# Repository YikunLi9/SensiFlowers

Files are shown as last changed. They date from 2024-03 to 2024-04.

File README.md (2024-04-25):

# SensiFlowers

## What the project does?

This project is an indoor artwork that connects with the environment and presents the data to the user in the form of art. The product will collect temperature and humidity of indoor environment through DTH-22 sensor, and display the data using the mechanical flower opening degree and color temperature of rgb light effect.

The whole product consists of three mechanical flowers and a wooden structure, as shown below:

<div align="center">
  SensiFlowers
</div>

The color of each flower in working mode represents a different data environment, with green representing carbon dioxide, red representing temperature, and blue representing humidity. As the ambient value increases, the color temperature will change from light to dark, and the flowers will gradually change from crouching to fully open.

## Why the project is useful?

We designed this project to fill a gap in the artistic emotional value of environmental monitors currently on the market. Most of the environmental data measurement devices on the market, only through a simple digital way, will measure the environmental data to express, which may lack a spiritual aesthetic, difficult to bring users a spiritual level of pleasure. 

Therefore, this product completes the measurement and display of environmental data through the artistic expression form of mechanical flower and lamp effect, and has a certain physical significance and practical value at the same time, it can also be used as an art decoration, placed in the living room or hung on the wall, bringing certain aesthetic value.

## How We Design？

### Initial Concept and Prototyping
The initial design concept focused on integrating natural elements, specifically using the imagery of a blooming flower to represent and interact with environmental data. Initial prototypes utilized thermally responsive metals to simulate the blooming process. However, this approach was found to interfere with the accurate monitoring of environmental conditions, as the device's primary function was compromised by the temperature sensitivity of the materials.

### Shift to Origami Modelling
To achieve a more reliable and aesthetically pleasing design, the development shifted towards origami modeling. This approach aimed to abstractly and artistically replicate the dynamic nature of a blooming flower, enhancing both visual appeal and functional reliability. Initial attempts to implement a hinged mechanism for transformation proved too complex and fragile for practical application.

<div align=center>
  Shift to Origami Modelling
</div>

### Material Innovation
The design evolved through a focus on material innovation. By integrating wooden panels with elastic TPU materials, the device was endowed with the necessary flexibility to mimic origami's bending and folding capabilities without compromising durability. This combination allowed significant bending angles while maintaining a robust structure within each modular unit.

<div align=center>
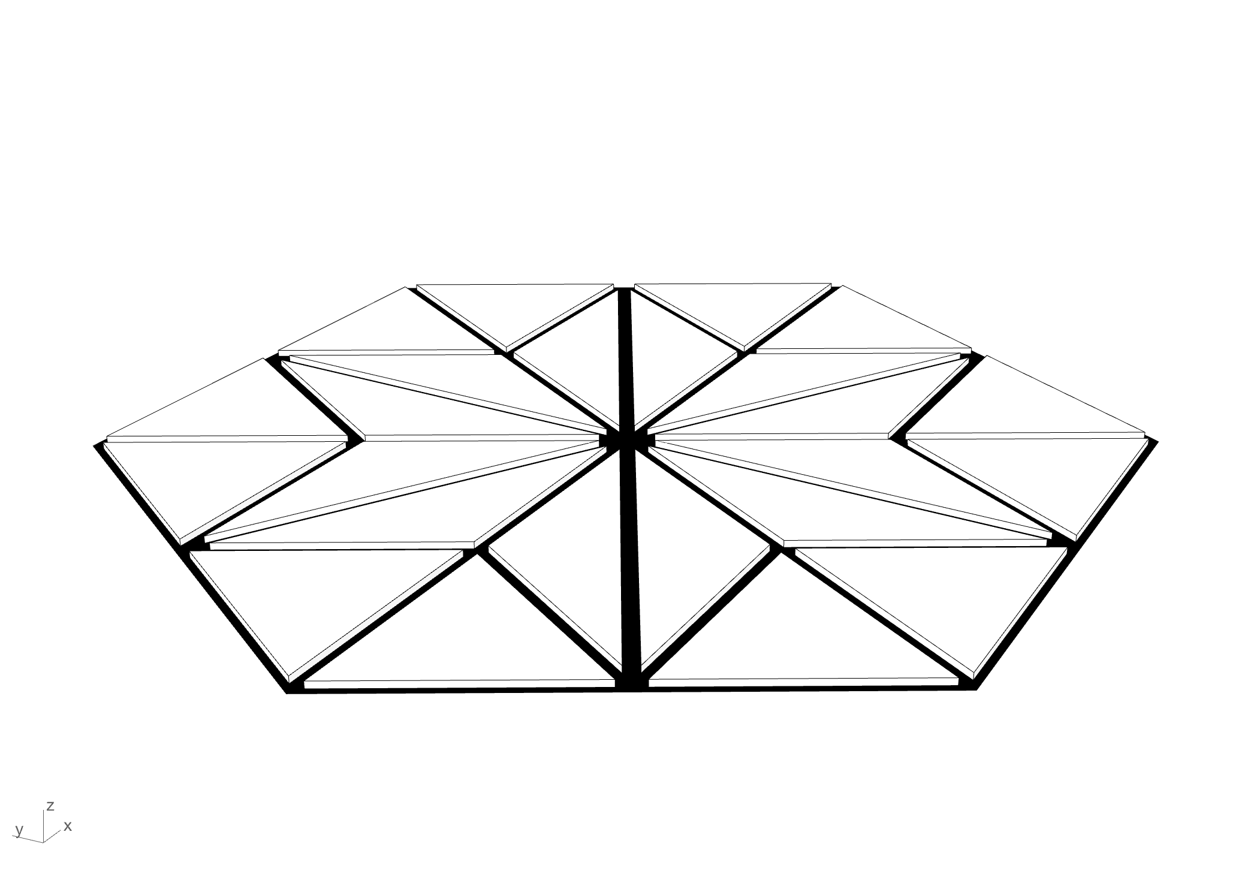
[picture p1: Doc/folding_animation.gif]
Material Innovation
  
</div>

### Development of the Operational Mechanism
The operational mechanism was inspired by classic gear transmission systems, transforming rotational motion into linear motion. This design utilized widely available motors to drive the expansion and contraction of the flower-like structures from multiple angles, achieving a single motor-driven mechanism that allowed each unit to expand and contract based on pre-designed parameters.

<div align=center>
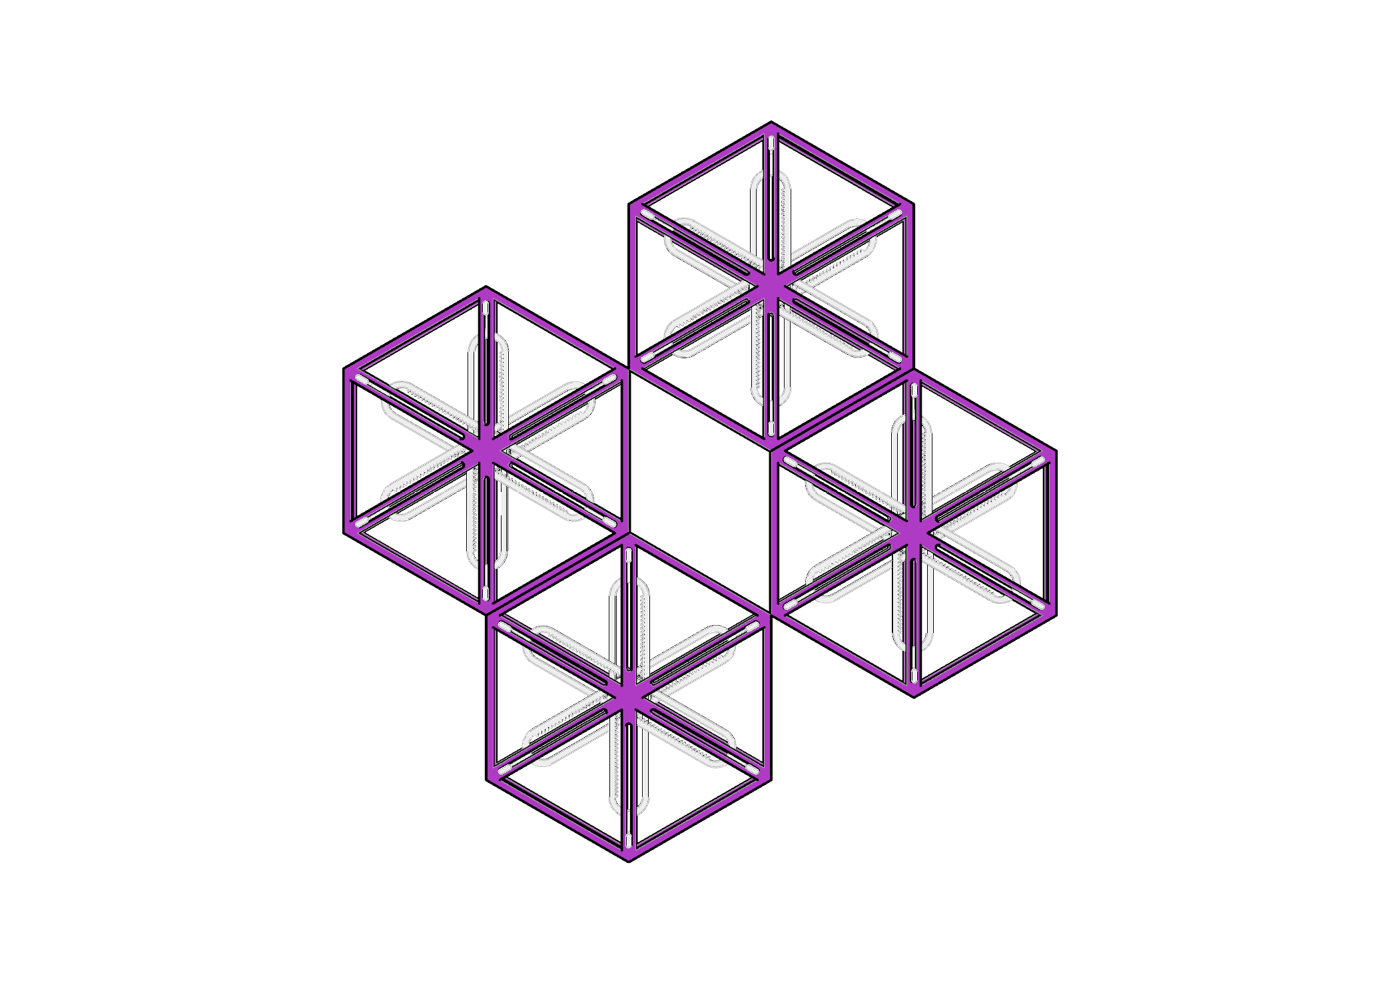
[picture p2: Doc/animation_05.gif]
Development of the Operational Mechanism
  
</div>

### Enclosure Design
The final stage involved designing an enclosure to house and integrate the individual units while concealing sensors and electrical components. Laser-cut wooden panels were used to create a harmonious geometric arrangement that not only supports the structural integrity but also complements the aesthetic value of the device.

<div align=center>
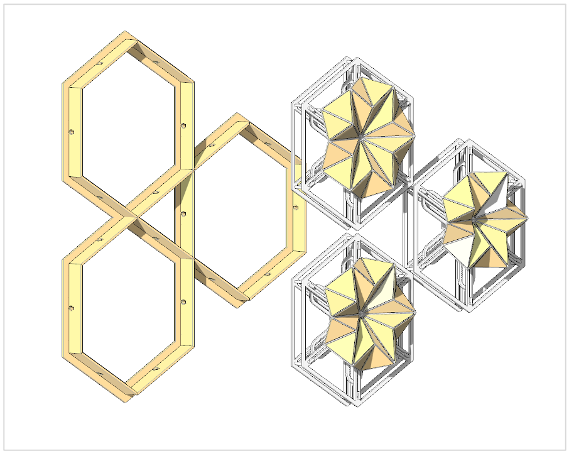
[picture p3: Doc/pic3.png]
Enclosure Design
  
</div>
## How this project works?

The project operates on data from the following sensors：

| Environment Data | Sensor |
| --- | --- |
| Temperature & Humidity | DHT22  |
| Carbon Dioxide Concentration | MQ135  |

And we set different ranges for these three environmental data to control the opening and closing of the mechanical flowers:

| Environment Data  | Upper Threshold of Optimal Range | Lower Threshold of Optimal Range |
| --- | --- | --- |
| Temperature | 30 | 20 |
| Humidity | 80 | 30 |
| CO2 Concentration | 1000 | 350 |

The mechanical flowers will fully open or close when the values exceed or fall below these thresholds. Simultaneously, the color temperature of the LEDs will vary within the following range:

| Environment Data  | Base Colour | Upper Threshold (RGB) | Lower Threshold (RGB) |
| --- | --- | --- | --- |
| Temperature | Red | 255, 0, 0 | 255, 50, 0 |
| Humidity | Blue | 0, 0, 255 | 80, 80, 255 |
| CO2 Concentration | Green | 0, 255, 0 | 0, 255, 50 |

## How users can get started with the project?

The use of this product is very simple, you only need to plug the power cord into the socket and turn on the power supply. The processing and measurement of the data is carried out locally, without any network connection, and the user does not need to perform any assembly and other operations. Environmental data can be read from the color and openness of flowers.

## Team members & Product help

A total of 4 team members completed the development of this product. Yuhang Lei completed the basic concept design of the product and the task assignment of the team, and undertook the welding task in the assembly process. Yikun Li compiled and debugged the development code of the single chip computer program, and gave guiding opinions on the form of data expression. Tianming Liu completed the design of the mechanical flower gear transmission group, and completed the 3d modeling and cutting of the gear group and the wooden shape. Zhouyu Jiang is responsible for the spraying of mechanical flower surface paint and hardware assembly, in addition to market research and follow-up product service research.

If you have further inquiries about our product and services or other aspects, you can communicate with any team member through github private message to get detailed information or answers. The detail of product services would be talked later in this read.me file.

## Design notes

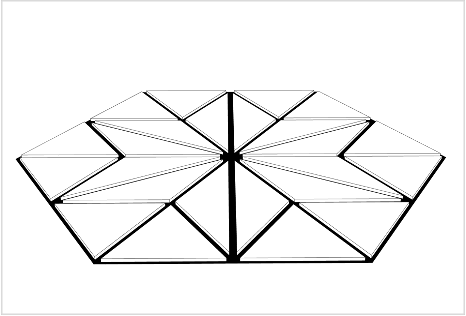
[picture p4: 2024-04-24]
Doc/ani.gif

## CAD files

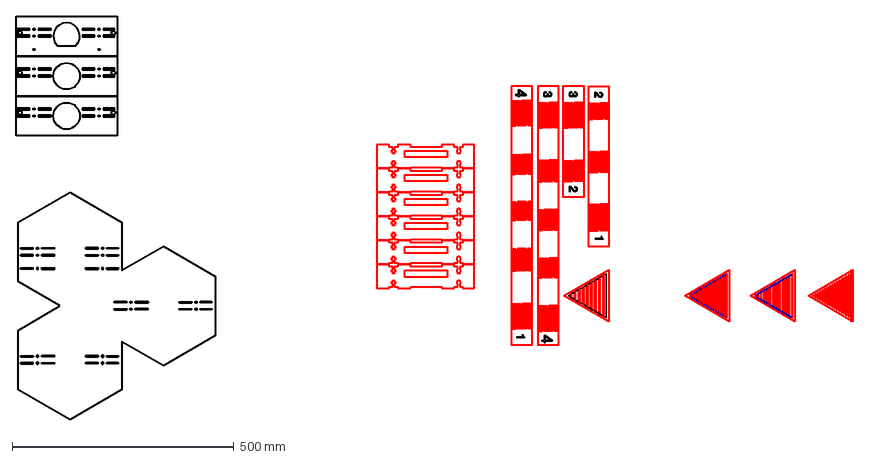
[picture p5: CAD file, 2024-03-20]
Model/LaserCut_Framework.dxf
1887.2 x 910.2 mm

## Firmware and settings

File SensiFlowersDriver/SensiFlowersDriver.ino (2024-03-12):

#include <DHT.h>
#include <Adafruit_NeoPixel.h>
#include <Servo.h>
#include <MQ135.h>


#define LED_PIN_1 3  // Pin of first LED
#define LED_PIN_2 4  // Pin of second LED
#define LED_PIN_3 5  // Pin of third LED
#define LED_COUNT 3  // number of LED in every device

#define DHTPIN 12 // Pin of DHT22 sensor

#define TEMPPIN 9 // Pin of temperature servo
#define HUMIPIN 10  // Pin of humidity servo 
#define CO2PIN 11 // Pin of CO2 servo

#define DHTTYPE DHT22 // type of DHT
#define PIN_MQ135 A2  // Pin of CO2 sensor

// Setup the Adafruit NeoPixel library with the LED count, pin, and color order
Adafruit_NeoPixel strip1(LED_COUNT, LED_PIN_1, NEO_GRB + NEO_KHZ800);
Adafruit_NeoPixel strip2(LED_COUNT, LED_PIN_2, NEO_GRB + NEO_KHZ800);
Adafruit_NeoPixel strip3(LED_COUNT, LED_PIN_3, NEO_GRB + NEO_KHZ800);

// Initialize sersons and servos
DHT dht(DHTPIN, DHTTYPE);
MQ135 mq135_sensor(PIN_MQ135);
Servo servo_temp;
Servo servo_humi;
Servo servo_co2;

// Save postion of servos in global variables
float pos_t;
float pos_h;
float pos_c;

void setup() {
  // Initialize the serial port
  Serial.begin(9600);
  // Initialize the DHT sensor
  dht.begin();

  // Attach the servos to the correct pins and PWM range
  servo_temp.attach(TEMPPIN, 500, 1800);
  servo_humi.attach(HUMIPIN, 500, 1800);
  servo_co2.attach(CO2PIN, 500, 1800);

  // Initialize the Adafruit NeoPixel library
  strip1.begin();
  strip2.begin();
  strip3.begin();

  // Set to zero
  Serial.println("Zero!");
  RGB_control(0, 0, 0);
  servo_temp.write(0);
  servo_humi.write(0);
  servo_co2.write(0);

  // Set the initial values for the servos
  pos_t = 0;
  pos_h = 0;
  pos_c = 0;

  // boot up animation and test
  for(int i = 0; i <= 100; i++){
    RGB_control(i * 0.1 + 20, i * 0.5 + 30, i * 6.5 + 350);
    Servo_control(i * 0.1 + 20, i * 0.5 + 30, i * 6.5 + 350);
    delay(30);
  }
  // Serial.println("over");
  // delay(10000);
}

void loop() {
  // Read the temperature, humidity, and ppm from sensors
  float t = dht.readTemperature();
  float h = dht.readHumidity();
  float ppm = mq135_sensor.getCorrectedPPM(t, h);

  // Serial.println(dht.readTemperature());
  // Serial.println(dht.readHumidity());
  // Serial.println(mq135_sensor.getRZero());

  // Set the RGB strip and servo values
  RGB_control(t, h, ppm);
  Servo_control(t, h, ppm);

  // loop per 30 seconds
  delay(10000);
}

/// @brief control RGB strip based on data
/// @param t temperature
/// @param h humidity
/// @param ppm co2 value(ppm)
void RGB_control(float t, float h, float ppm){
  // Set the RGB strip values based on the temperature
  if(t > 30){
    strip1.setPixelColor(0, 0, 255, 0);
    strip1.setPixelColor(1, 0, 255, 0);
    strip1.setPixelColor(2, 0, 255, 0);
    strip1.show();
  }else if(t < 20){
    strip1.setPixelColor(0, 50, 255, 0);
    strip1.setPixelColor(1, 50, 255, 0);
    strip1.setPixelColor(2, 50, 255, 0);
    strip1.show();
  }else{
    int temp_g = 0;
    temp_g = (30 - t) * 50 / 10;
    strip1.setPixelColor(0, temp_g, 255, 0);
    strip1.setPixelColor(1, temp_g, 255, 0);
    strip1.setPixelColor(2, temp_g, 255, 0);
    strip1.show();
  }

  // Set the RGB strip values based on the ppm
  if(ppm >= 1000){
    strip2.setPixelColor(0, 255, 0, 0); 
    strip2.setPixelColor(1, 255, 0, 0); 
    strip2.setPixelColor(2, 255, 0, 0); 
    strip2.show();
  }else if(ppm <= 350){
    strip2.setPixelColor(0, 255, 0, 50);
    strip2.setPixelColor(1, 255, 0, 50);
    strip2.setPixelColor(2, 255, 0, 50);
    strip2.show();
  }else{
    int co2_b = 0;
    co2_b = (ppm - 350) / 650 * 50;
    strip2.setPixelColor(0, 255, 0, 50 - co2_b);
    strip2.setPixelColor(1, 255, 0, 50 - co2_b);
    strip2.setPixelColor(2, 255, 0, 50 - co2_b);
    strip2.show();
  }
  
  // Set the RGB strip values based on the humidity
  if(h > 80){
    strip3.setPixelColor(0, 0, 0, 254);
    strip3.setPixelColor(1, 0, 0, 254);
    strip3.setPixelColor(2, 0, 0, 254);
    strip3.show();
  }else if(h < 30){
    strip3.setPixelColor(0, 80, 80, 255);
    strip3.setPixelColor(1, 80, 80, 255);
    strip3.setPixelColor(2, 80, 80, 255);
    strip3.show();
  }else{
    int humi_g = 0;
    int humi_r = 0;
    humi_g = (80 - h) * 80 / 50;
    humi_r = (80 - h) * 80 / 50;
    strip3.setPixelColor(0, humi_g, humi_r, 255);
    strip3.setPixelColor(1, humi_g, humi_r, 255);
    strip3.setPixelColor(2, humi_g, humi_r, 255);
    strip3.show();
  }
}

/// @brief control servo position based on data
/// @param t temperature
/// @param h humidity
/// @param ppm co2 value(ppm)
void Servo_control(float t, float h, float ppm){
  // Set the servo values based on the temperature
  if(t >= 30){
    float temp = 180;
    smoother(servo_temp, temp, &pos_t);
  }else if(t <= 20){
    float temp = 0;
    smoother(servo_temp, temp, &pos_t);
  }else{
    float temp = (t - 20) / 10 * 180;
    smoother(servo_temp, temp, &pos_t);
  }

  // Set the servo values based on the humidity
  smoother(servo_humi, h * 1.8, &pos_h);

  // Set the servo values based on the ppm
  if(ppm >= 1000){
    float temp = 180;
    smoother(servo_co2, temp, &pos_c);
  }else if(ppm <= 350){
    float temp = 0;
    smoother(servo_co2, temp, &pos_c);
  }else{
    float temp = (ppm - 350) / 650 * 180;
    smoother(servo_co2, temp, &pos_c);
  }
}


/// @brief smooth the servo rotating
/// @param servo servo you want to control
/// @param tar target postion
/// @param prev pointer of previous position(which is pos_t, pos_h, pos_c)
void smoother(Servo servo, float tar, float* prev){
  if(*prev > tar){
      for(*prev; *prev > tar; *prev = (*prev * 100 - 1) / 100){
        servo.write(*prev);
        // delay(1);
      }
    }else if(*prev < tar){
      for(*prev; *prev < tar; *prev = (*prev * 100 + 1) / 100){
        servo.write(*prev);
        // delay(1);
      }
    }
}

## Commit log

2024-03-20 3D Model of Flower Base
2024-03-20 Laser Cut File for Back Framework
    [LaserCut_Framework.dxf]
